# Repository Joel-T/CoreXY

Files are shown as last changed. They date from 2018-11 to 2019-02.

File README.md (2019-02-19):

# Belted Core XY
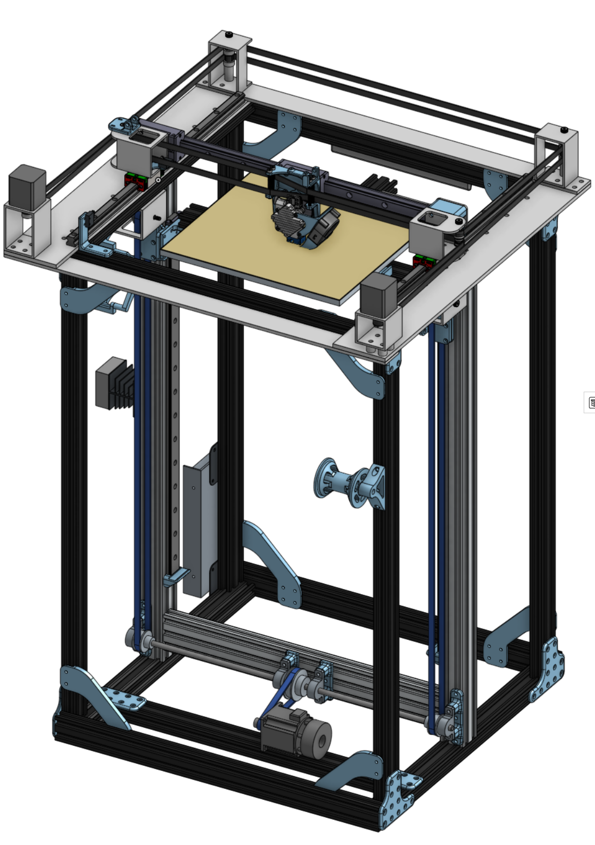
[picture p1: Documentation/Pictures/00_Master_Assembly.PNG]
Core XY Printer Assembly


Documentation, plans, and files  for the Belted Core XY.
## Table of Contents
| Topic  | Resource |
|:---:|:---:|
|Overview|[Link](README.md)  |
|BOM |[Link](Documentation/BOM.md)  |
|Parts |[Link](Parts) |
|Configuration| [Link](Documentation/Configuration.md) |
|Wiring Guide (WIP) | [Link](Documentation/Wiring.md) |
|Write-up| [Link](Documentation/) |

## Overview
The design intent with the Belted Core XY was to create a robust motion platform that can be configured for a number of applications such as 3D printing, light milling, plotting, and laser etching. For the most part it was designed with 3D printing in mind. I plan to completely remodel the Belted Core XY in Fusion when I get the chance so that I can offer more than a step file.
### 3D printer Design Intent:
1. Core XY Kinematics
2. Rigid Frame
3. Ability to change tool
4. Linear rails 
5. Belted bed
6. Z-Stepper w/ brake
7. Aluminum for all major parts of the motion platform
8. Swappable Bed
9. 300mm^2 build plate 
10. 120v AC bed heater

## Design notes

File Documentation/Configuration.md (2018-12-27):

## Configuration for Duet
This section will cover the initial configuration of the Duet controller for the printer, for problems and tuning go [here](Documentation/Issues.md) and for setting up a new Duet [here](https://duet3d.dozuki.com/Guide/1.+Getting+Connected+to+your+Duet/7).

To start we use the [RepRap Config Tool](https://configurator.reprapfirmware.org/Start) to generate the initial configuration file. 

1. First start by selecting the custom configuration option and click next.
2. On this page enable the Read config-override.g option and make sure to select the CoreXY Geometry option. For the axis min and max see the following table: 

| Axis  | Position |
| :--:  | :---: |
| X Min | 0 |
| X Max | 330 |
| Y Min | -40 |
| Y Max | 400 |
| Z Min | 0 |
| Z Max | 550 |

3. On the following page the steppers are configured. The direction is dependent of how you plug the steppers into the Duet so for now just leave them all as Forwards, this can be changed anytime from the web interface or by reversing the plug on the steppers. Note: never insert or remove a stepper while the Duet is powered or you risk frying the driver! For this section I am going to assume 1.8* steppers for the X, Y, and Z, a 0.9* stepper for the E, and x16 microstepping interpolated to x256. The settings are as follows:

| Drive | Steps per mm | Max Speed Change (mm/s) | Max Speed (mm/s) | Acceleration (mm/s<sup>2</sup>) | Motor Current (mA) | Motor Driver |
| :---: | :---: | :---: | :---: | :---: | :---: | :---: |
| X | 80 | 10 | 250 | 500 | 1200 | 0 (X) |
| Y | 80 | 10 | 250 | 500 | 1200 | 1 (Y) |
| Z | 100 | 0.2 | 10 | 20 | 1800 | 2 (Z) |
| E | 837 | 2 | 20 | 250 | 1000 | 3 (E0) |

4. The Z-Probe uses the nozzle itself as the contact there is no X or Y offset so that can be left at 0 mm. For the probe type select the "Smart Effector or Piezo" and set the trigger height to -0.2 mm. This value is how you tune your first layer and like all other settings this can be adjusted later through the web interface. Make sure that it is set as a negative value or after probing your hotend **WILL** crash into the bed. I set the Trigger value to 800 so that if the piezo disk has some pressure on it or there is some electrical interference the probe isn't falsely triggered. Recovery time can be left at 0.4 seconds. The Homing Preferences can also be left at their defaults. Endstop configuration is a pretty straight forward affair. A left-front origin is used and the configuration is as follows:

| Axis | Endstop Type | Endstop Location |
| :--: | :---: | :---: |
| X  |  Active high | At low end |
| Y  |  Active high | At low end |
| Z  | Z-Probe | At low end |

5. The heater settings are simple even with the bed heater being controlled by a SSR. Make sure for the General settings that "Heated Bed" is checked and set to Bang-Bang for control method. For the rest of the heater configuration it is as follows:

| Heater | Type | Temp. Limit | PWM Limit | R25 | β | C | Sensor Channel |
| :----: | :--: | :---: | :---: | :-: | :-:| :-: | :---: |
|  Bed | Heated Bed | 175 | N/A | 100000 | 3950 | 0 | Bed Thermistor |
| E0 | Nozzle | 400 | 100 | N/A | N/A | N/A | MAX31856 on CS1 |

6. On the next page the mesh bed compensation is set up. The print head has a workspace that exceeds the size of the bed so it is important when setting up the mesh leveling that you ensure the probing points are on the bed. For this printer it is as follows:

| X Min | X Max | Y Min | Y Max | Grid Spacing |
| :---: | :---: | :---: | :---: | :---: |
|  15 |  295  |  15 |  295  | 20 |

7. On this page you can name the printer as you see fit and you can also set up the wifi info now to connect to the network that the printer will be on. I advise that after the Duet is setup and configured to go into your router and assign the Duet a fixed IP so that you can easily make a bookmark to the web interface.
8. For the final page we will be configuring the cooling fans and the z axis brake. There should be three fans, 0, 1, and 2, if there isn't just click the add fan button in the upper right. Fan 0 will be the part cooling fan, fan 1 the hotend fan, and fan 2 the brake. This is set up as such:

| Name | Value | Inverted | Frequency | Thermostatic Control | Monitored Heaters | Thermostatic Mode Trigger Temp. |
| :--: | :---: | :---: | :---: | :---: | :---: | :---: |
| Fan0 | 0 | No | 500 | No | N/A | N/A |
| Fan1 |  100  | No | 500 | Yes | E0 | 45 |
| Fan2 | 0 | No | 500 | No | N/A | N/A |

9. Finally click finish and download the bundle as a zip file.

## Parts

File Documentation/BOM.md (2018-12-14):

## Bill of Materials

|  | Part Name | Number Needed |
|:---:|:---:|:---:|
| 2040 Extrusion |  |  |
|  | 210mm | 1 |
|  | 415mm | 1 |
|  | 470mm | 1 |
|  | 500mm | 8 |
|  | 550mm | 8 |
|  | 800mm | 4 |
| 2060 Extrusion |  |  |
|  | 470mm | 1 |
| 4040 Extrusion |  |  |
|  | 800mm | 2 |
| Aluminum Plate |  |  |
|  | 3.5" x 24" x 1/4" | 2 |
|  | 40mm x 48" x 5mm | 2 |
|  | 12" x 12" x 3/8" Mic6 | 1 |
|Aluminum Tubing|  |  |
|  | 2" x 2" x 24" | 1 |
|  | 2" x 3" x 12" | 1 |
| Linear Rails |  |  |
|  | HGH 15 | 2 |
|  | HGH 20 | 1 |
|  | MGW 12 | 2 |
| Linear Rail Block |  |  |
|  | HGH 15 Square Low | 2 |
|  | HGH 20 Square Low | 2 |
|  | MGW 12 Long | 2 |
| Hardware |  |  |
|  | M4 Drop in nut | 72 |
|  | M5 Drop in nut | 24 |
|  | M4 LP nut | 1 pack |
|  | M5 LP nut | 1 pack |
|  | M6 LP nut | 4 |
|  | M6 nut | 22 |
|  | M8 LP nut | 2 |
|  | M2 x 12mm | 4 |
|  | M3 x 8mm | 8 |
|  | M3 x 12mm | 2 |
|  | M4 x 8mm | 72 |
|  | M4 x 10mm | 32 |
|  | M4 x 16mm | 30 |
|  | M4 x 45mm | 4 |
|  | M5 x 8mm | 5 |
|  | M5 x 10mm | 44 |
|  | M5 x 12mm | 12 |
|  | M6 x 16mm | 6 |
|  | M6 x 35mm | 16 |
|  | M6 x 45mm | 2 |
|  | M8 x 25mm | 2 |
|  | 1/4" Shoulder Screw 2" Shoulder | 4 |
|  | 1/4" Shoulder Screw 3-1/4" Shoulder | 2 |
|  | 10-24 Thin Nut | 6 |
|  | GT2 20 Tooth 9mm Belt 5mm Bore | 2 |
|  | GT2 20 Tooth 9mm Belt 6.35mm Bore | 6 |
|  | 1/2" Flange Bearing | 4 |
|  | M8 Rod 550mm | 1 |
|  | M8 Pillow Bearing | 4 |
|  | HTD 3M 16 Tooth 8mm Bore | 1 |
|  | HTD 3M 32 Tooth 8mm Bore | 2 |
|  | HTD 3M 48 Tooth 8mm Bore | 1 |
|  | HTD 3M 32 Tooth 6.35mm Bore | 2 |
|  | L Bracket Triple | 2 |
|  | Hidden Tee Nut | 28 |
|  | Spacer 6mm Bore 13mm Length | 4 |
|  | Spacer 6mm Bore 25mm Length | 4 |
|  | Spacer 1/4" Bore 1/2" Length | 4 |
|  | Spacer 1/4" Bore 1" Length | 2 |
|  | Thrust Bearing 1/4" Bore 5/8" OD 1/16" Thick | 10 |
|  | 608 Bearing | 2-4 |
|  | Titan Aero | 1 |
| Electronics |  |  |
|  | Duet | 1 |
|  | PT100 Daughter Board | 1 |
|  | Piezo20 or Universal Kit | 1 |
|  | Nema 17 Stepper 0.9* LP | 1 |
|  | Nema 17 Stepper 1.8* | 2 |
|  | Nema 23 Stepper w/ Brake | 1 |
|  | AC SSR | 1 |
|  | 4020 Blower Fan | 1 |
|  | Meanwell 350W PSU | 1 |
|  | Cooling Fan | 1 |
|  | NC Micro Switch | 2 |
| Printed Parts |  |  |
|  | Chain Link Pair | 18 |
|  | Corner Bracket | 4 |
|  | Corner Bracket Mirror | 4 |
|  | Corner Plate | 4 |
|  | Corner Pate Mirror | 4 |
|  | Bed Mount | 2 |
|  | Duet Fan Mount | 2 |
|  | Pillow Block Wide | 2 |
|  | Pillow Block Narrow | 2 |
|  | Straight Plate | 2 |
|  | Bed Stop | 2 |
|  | Fixed Bed Belt Clamp | 2 |
|  | Ribbed Bed Belt Clamp | 2 |
|  | Bed Thumb Screw | 2 |
|  | Bed Leveler | 2 |
|  | Spool Bearing | 2 |
|  | Bed Mount Wide | 1 |
|  | Rail Z Bed Left | 1 |
|  | Rail Z Bed Right | 1 |
|  | X Endstop | 1 |
|  | Y Endstop | 1 |
|  | Tube Mount | 1 |
|  | Cable Chain Hotend | 1 |
|  | Cable Chain Tubing | 1 |
|  | Hotend Fan | 1 |
|  | Titan Areo | 1 |
|  | Duet Board Mount | 1 |
|  | Nema 23 Mount | 1 |

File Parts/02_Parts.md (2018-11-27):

## Parts
All Parts are stored here for download. The Chainlink pair file is from the Maker's Tool Works Minimax 3D printer files, all other parts are my design. See the [BOM](Documentation/01_BOM.md) for the number of each part that is needed.

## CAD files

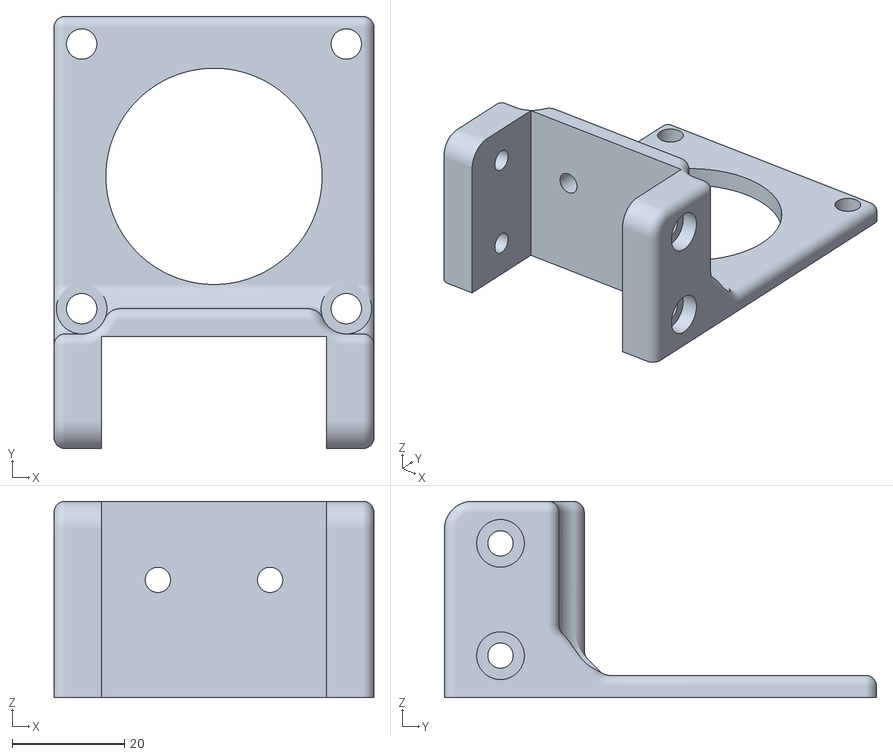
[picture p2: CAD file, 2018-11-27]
Parts/STL/Nema 23 mount.stl
57.0 x 77.0 x 35.0

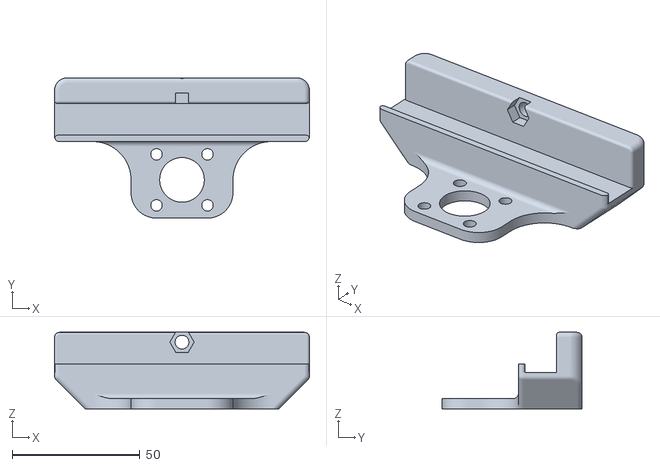
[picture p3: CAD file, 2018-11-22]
Parts/STL/Bed Mount Wide.stl
100.0 x 55.0 x 30.0

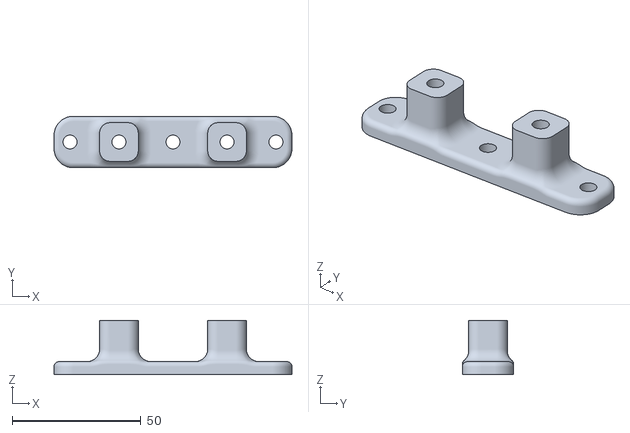
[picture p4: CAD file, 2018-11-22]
Parts/STL/Pillow Block Wide.stl
92.5 x 20.0 x 21.0

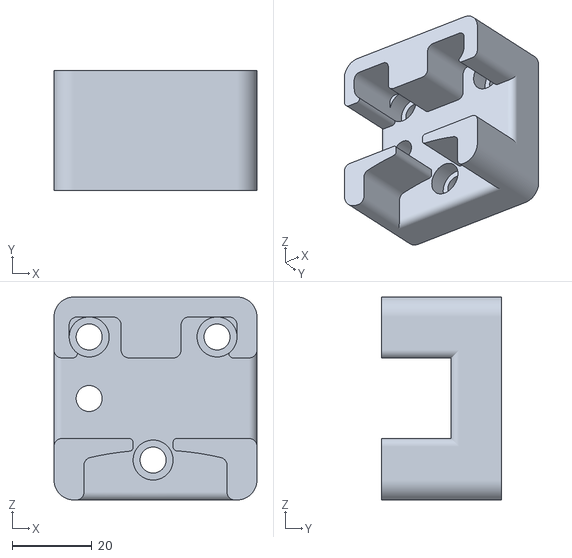
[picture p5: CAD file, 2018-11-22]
Parts/STL/Tubing Mount.stl
50.8 x 30.0 x 50.8

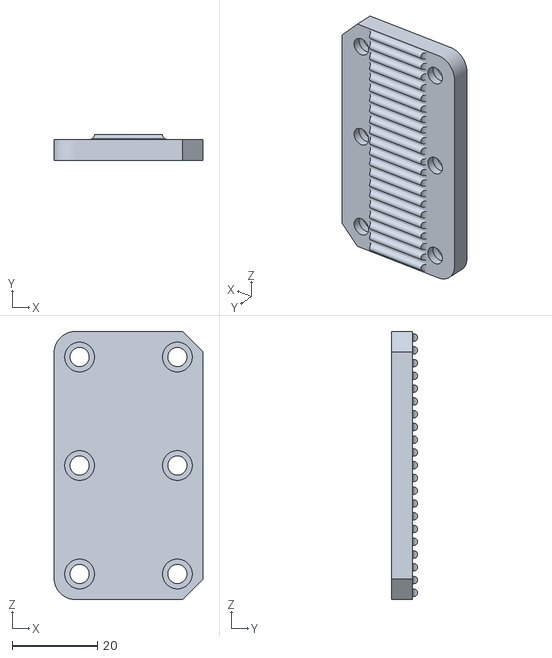
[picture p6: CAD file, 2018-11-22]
Parts/STL/Ribbed Clamp.stl
35.0 x 6.17 x 63.0

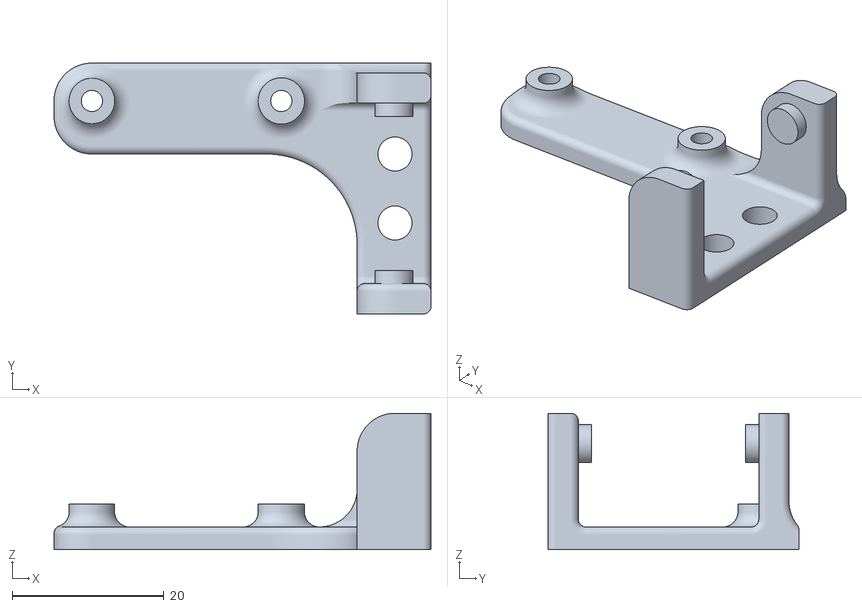
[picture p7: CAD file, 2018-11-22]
Parts/STL/Cable Chain Hotend.stl
49.8 x 33.1 x 18.0

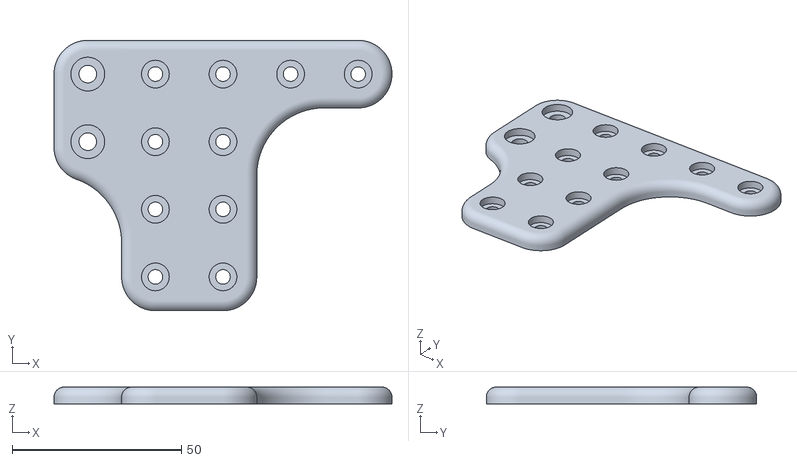
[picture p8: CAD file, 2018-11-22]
Parts/STL/Corner Plate Mirror.stl
100.0 x 80.0 x 5.00

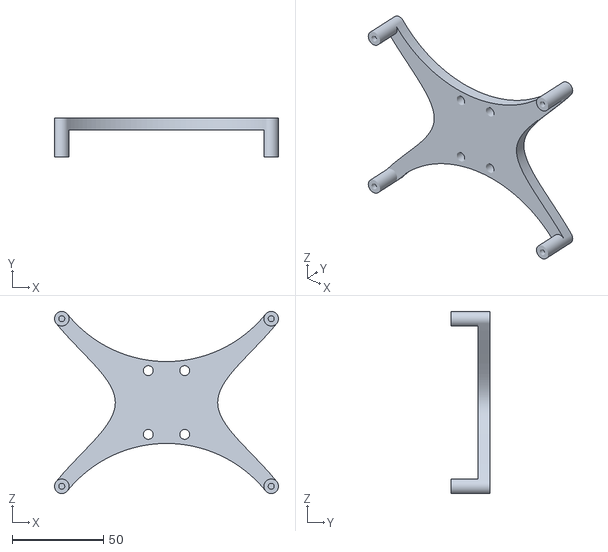
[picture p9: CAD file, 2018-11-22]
Parts/STL/Duet Mount.stl
123.0 x 21.5 x 100.0

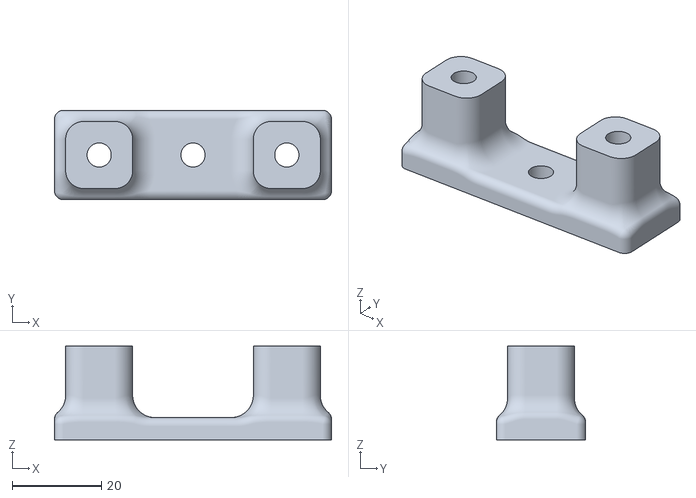
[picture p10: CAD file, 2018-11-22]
Parts/STL/Pillow Block Narrow.stl
62.0 x 20.0 x 21.0

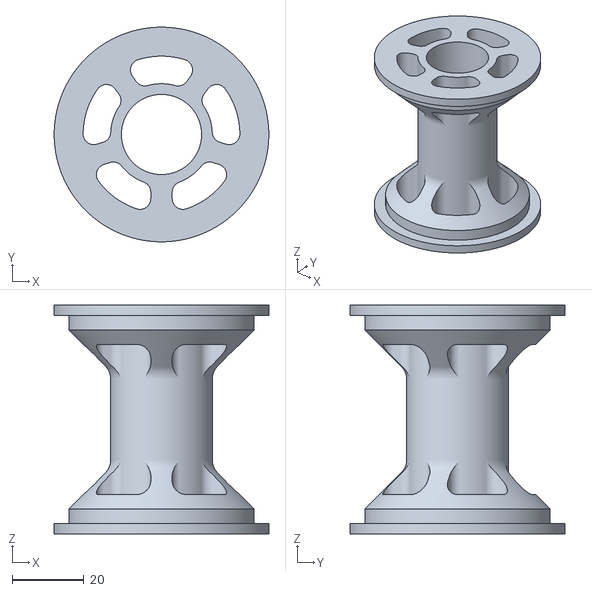
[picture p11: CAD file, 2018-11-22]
Parts/STL/Filament Bearing.stl
60.0 x 60.0 x 64.0

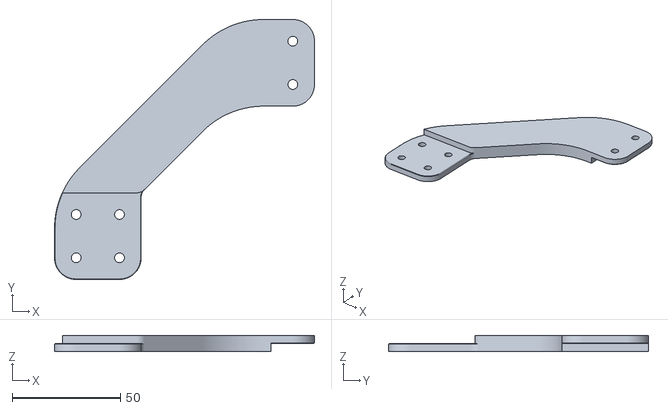
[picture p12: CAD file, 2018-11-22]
Parts/STL/Corner Bracket Mirror.stl
120.0 x 120.0 x 7.50

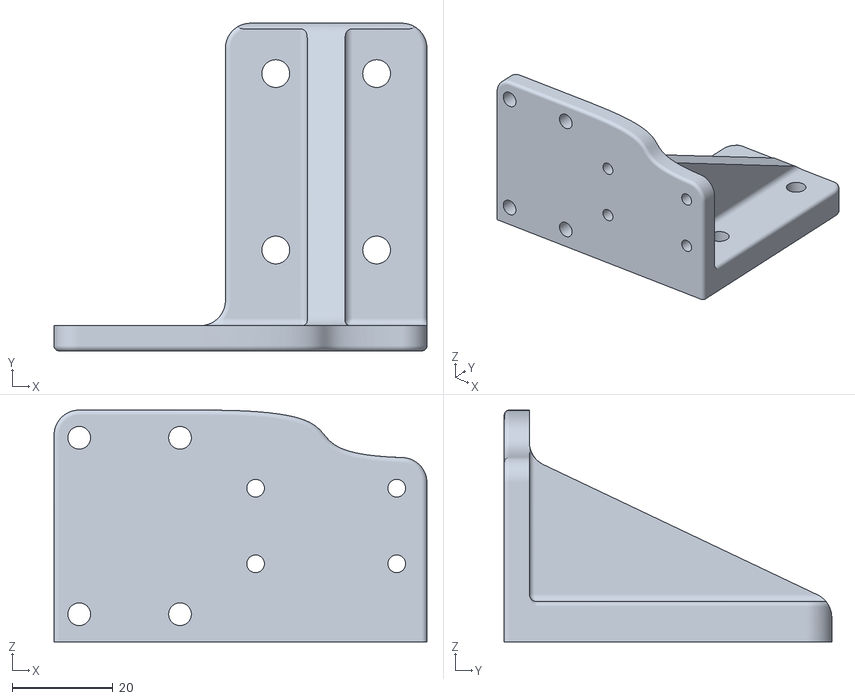
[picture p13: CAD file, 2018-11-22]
Parts/STL/Rail Z Bed Mount Right.stl
74.0 x 65.0 x 46.0

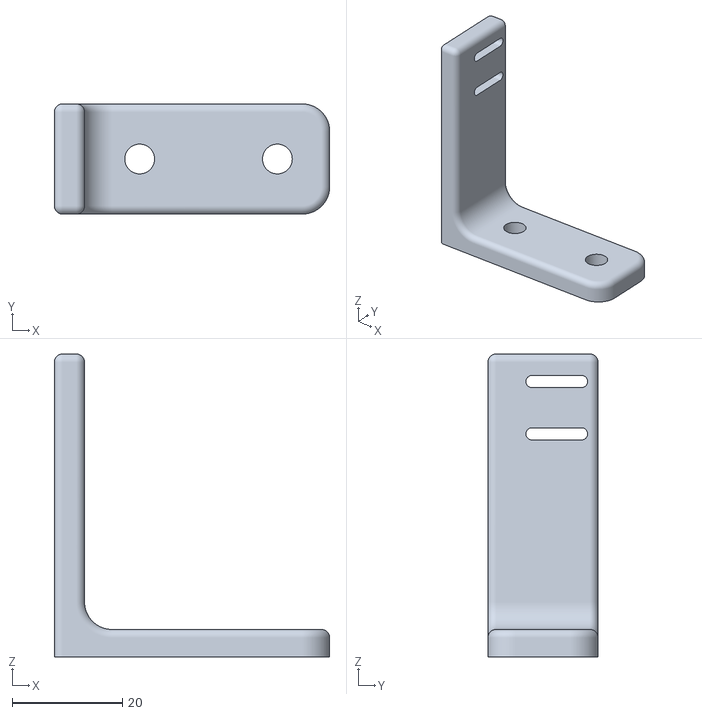
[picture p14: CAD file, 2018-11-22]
Parts/STL/Y End Stop.stl
50.0 x 20.0 x 55.0

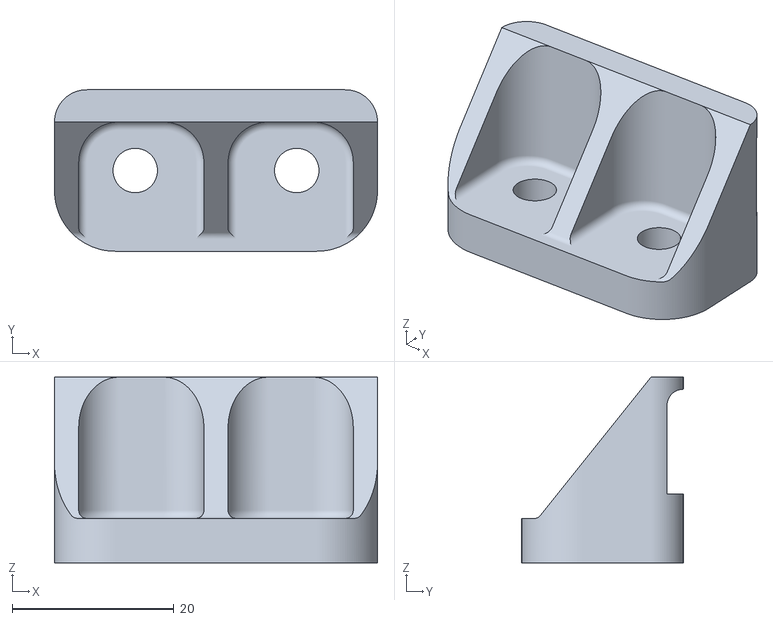
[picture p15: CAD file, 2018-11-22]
Parts/STL/Bed Stop.stl
40.0 x 20.0 x 23.0

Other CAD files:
Parts/STL/Corner Bracket.stl
Parts/STL/Corner Plate.stl
Parts/STL/Hotend Fan Mount.stl
Parts/STL/Bed Mount.stl
Parts/STL/Cable Chain Tubing.stl
Parts/STL/Duet Fan Mount.stl
Parts/STL/Fixed Clamp.stl
Parts/STL/Leveler.stl
Parts/STL/Rail Z Bed Mount Left.stl
Parts/STL/Screw Head.stl
Parts/STL/X End Stop.stl
Parts/STL/chainlink pair.STL

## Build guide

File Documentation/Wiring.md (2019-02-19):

## Wiring

This section will cover wiring up all of the electronics for the printer as well as any other accessories such as lights and fans.

### Overview
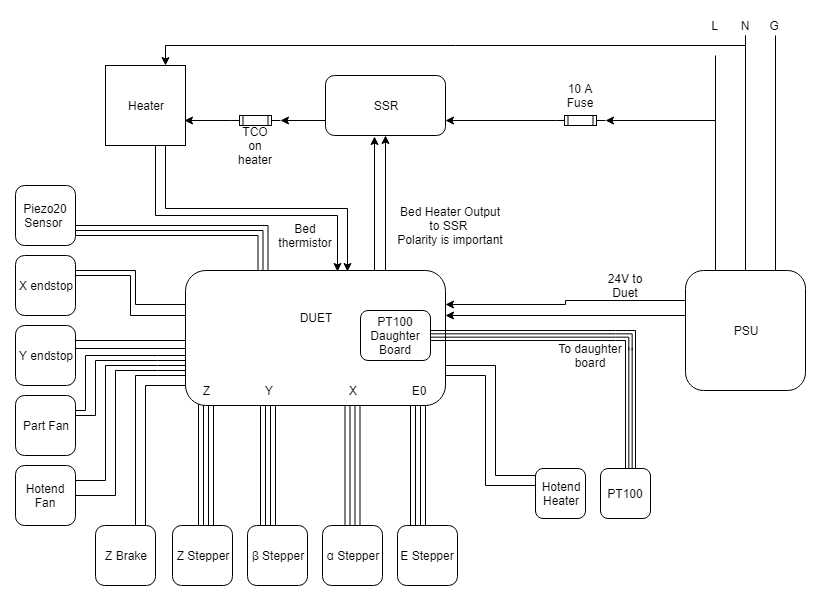
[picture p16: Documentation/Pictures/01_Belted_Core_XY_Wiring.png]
Core XY Printer Wiring


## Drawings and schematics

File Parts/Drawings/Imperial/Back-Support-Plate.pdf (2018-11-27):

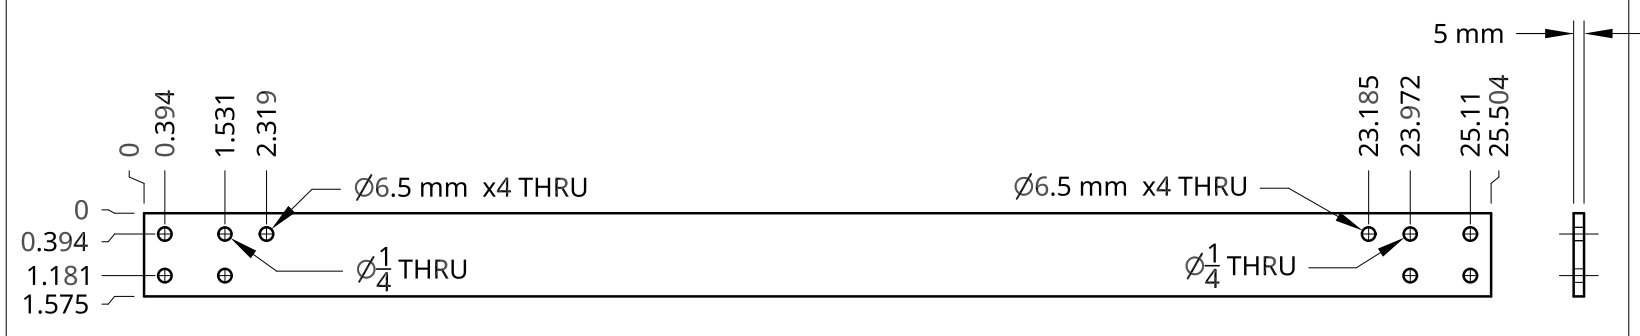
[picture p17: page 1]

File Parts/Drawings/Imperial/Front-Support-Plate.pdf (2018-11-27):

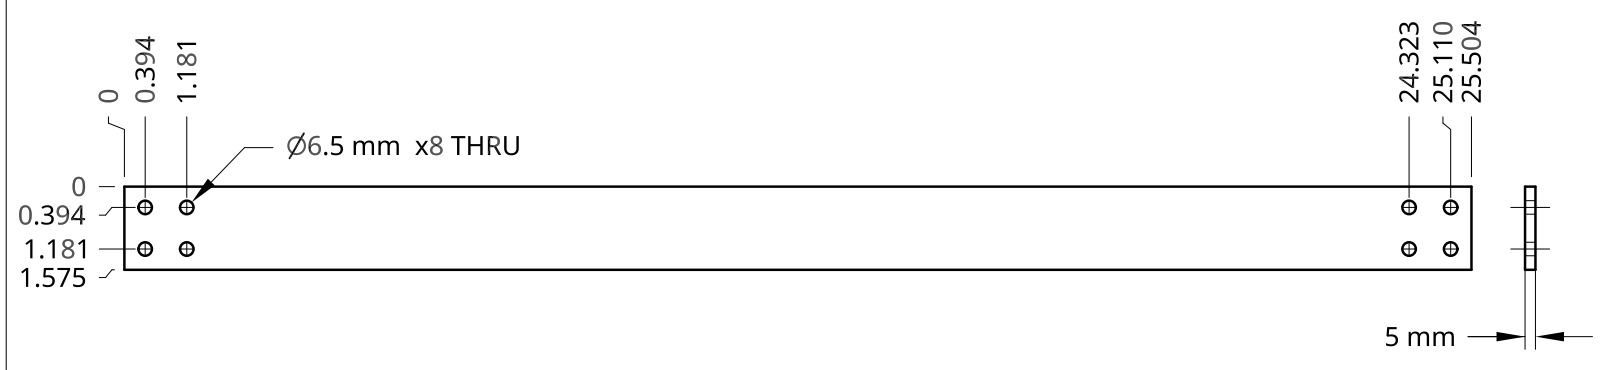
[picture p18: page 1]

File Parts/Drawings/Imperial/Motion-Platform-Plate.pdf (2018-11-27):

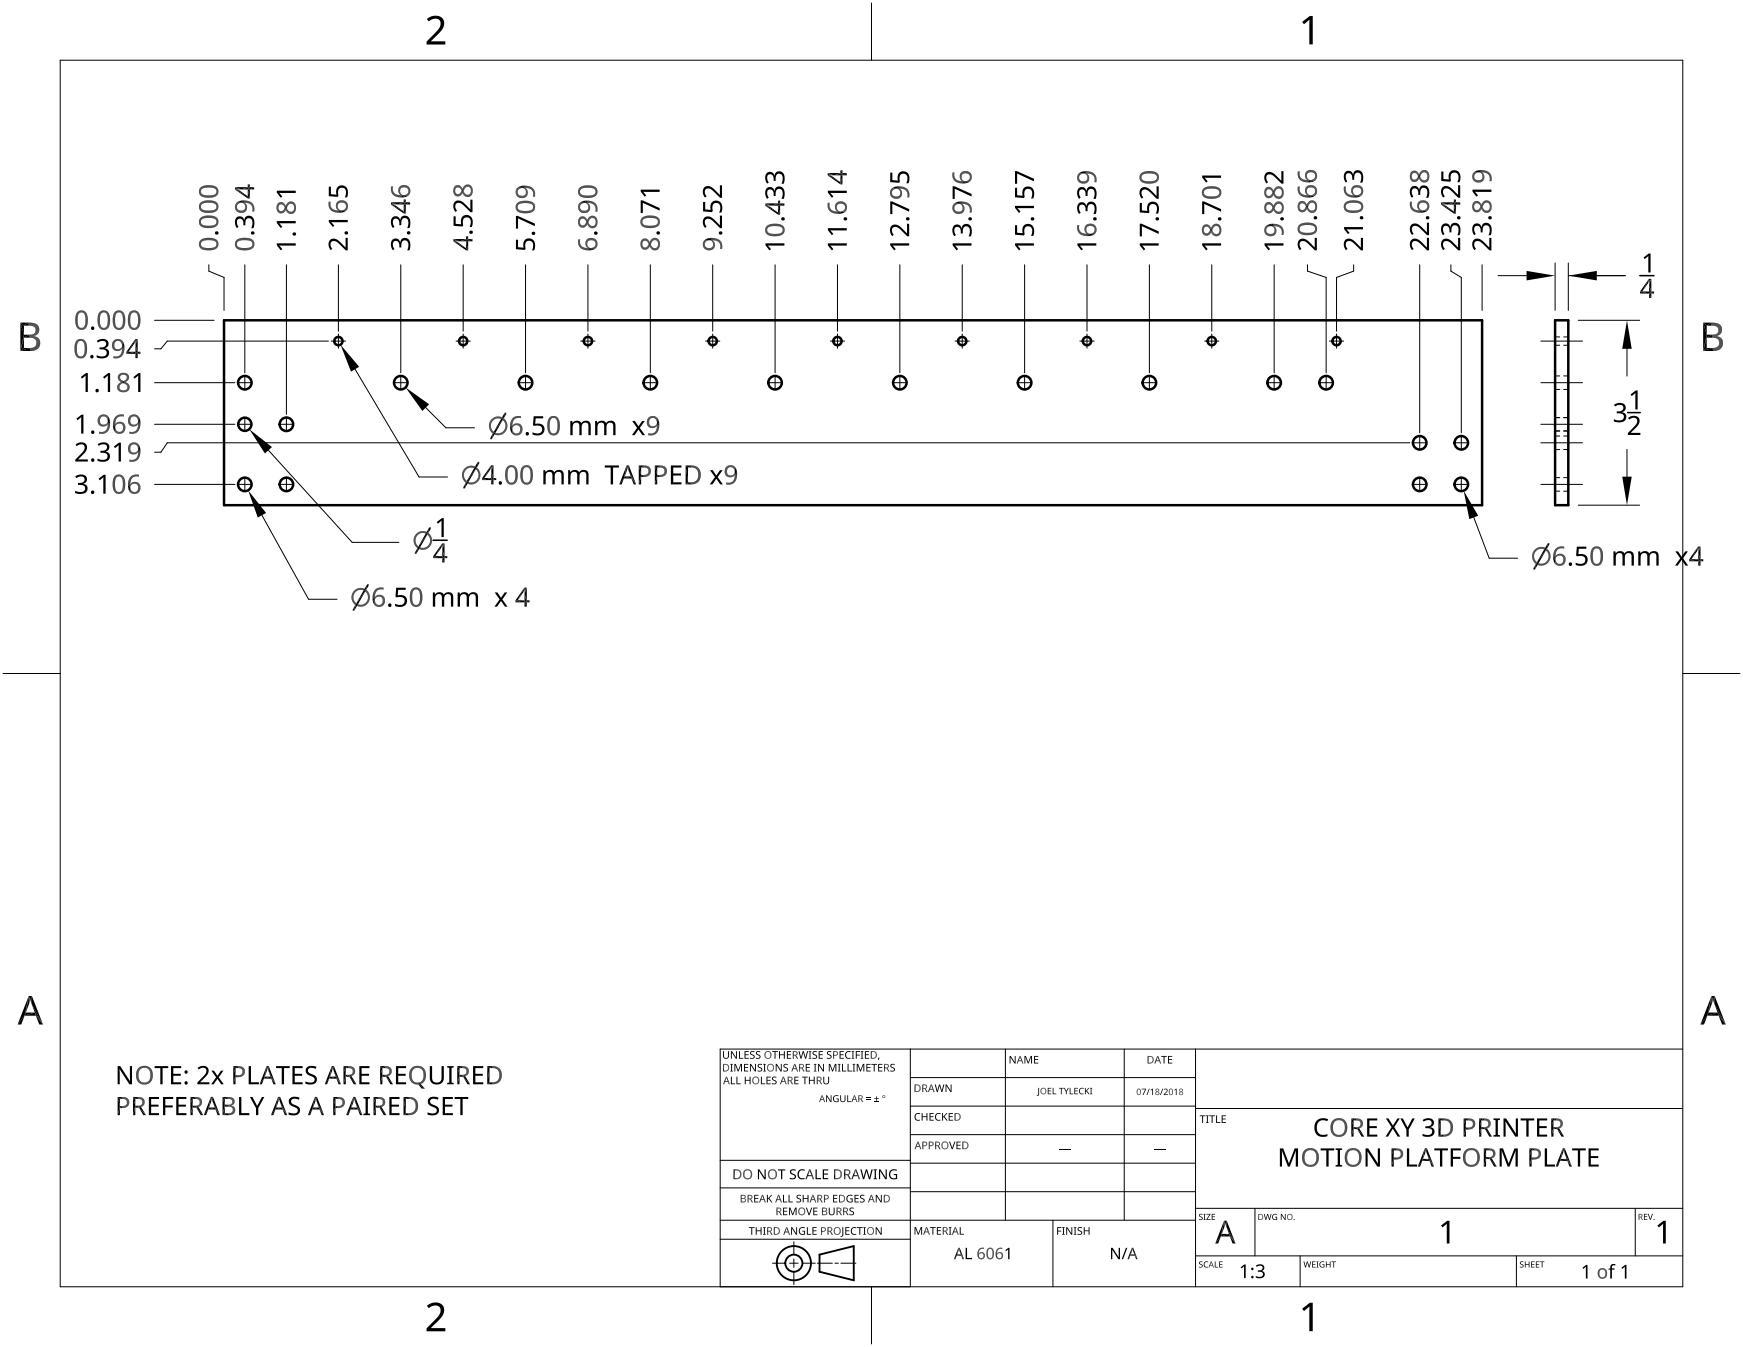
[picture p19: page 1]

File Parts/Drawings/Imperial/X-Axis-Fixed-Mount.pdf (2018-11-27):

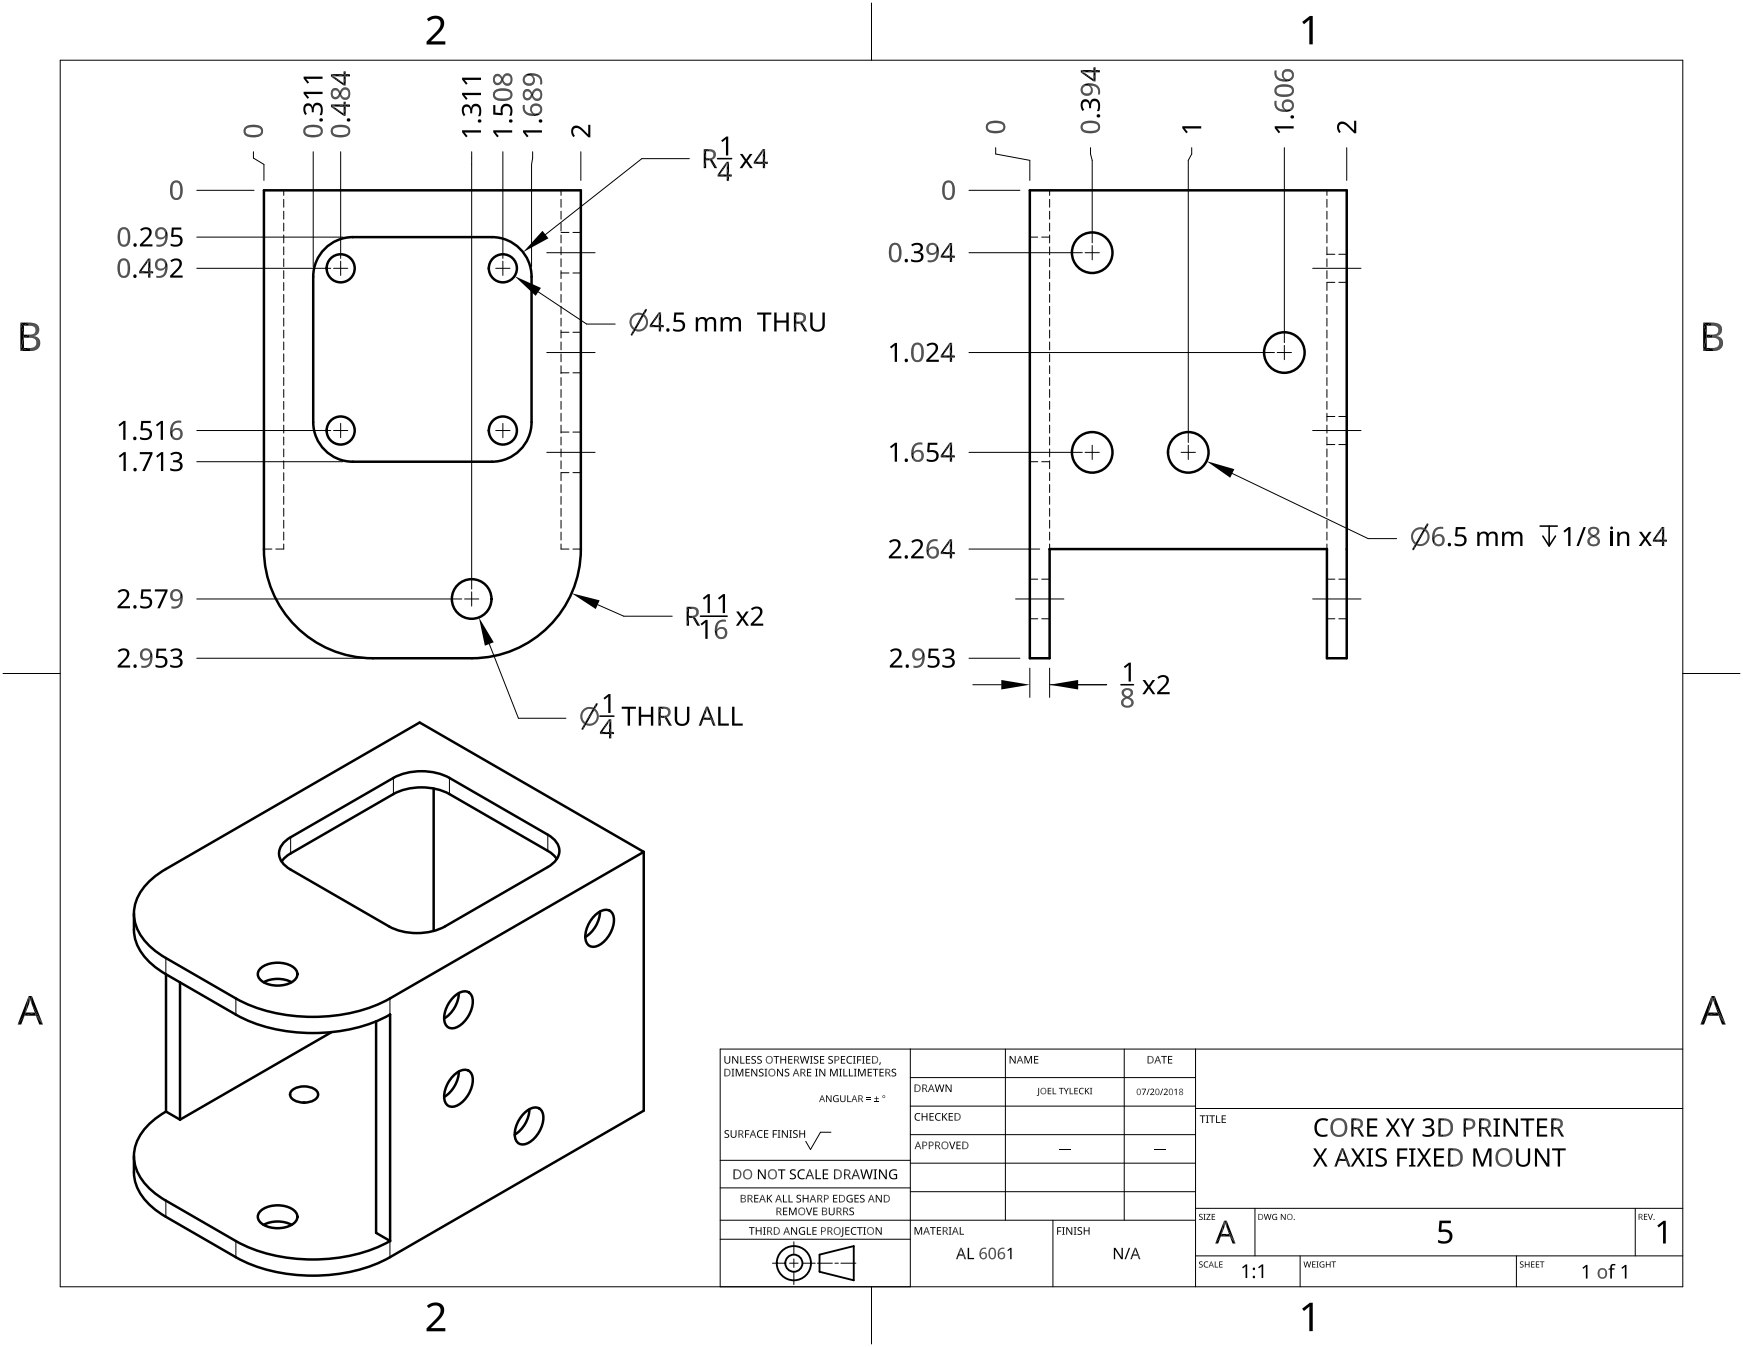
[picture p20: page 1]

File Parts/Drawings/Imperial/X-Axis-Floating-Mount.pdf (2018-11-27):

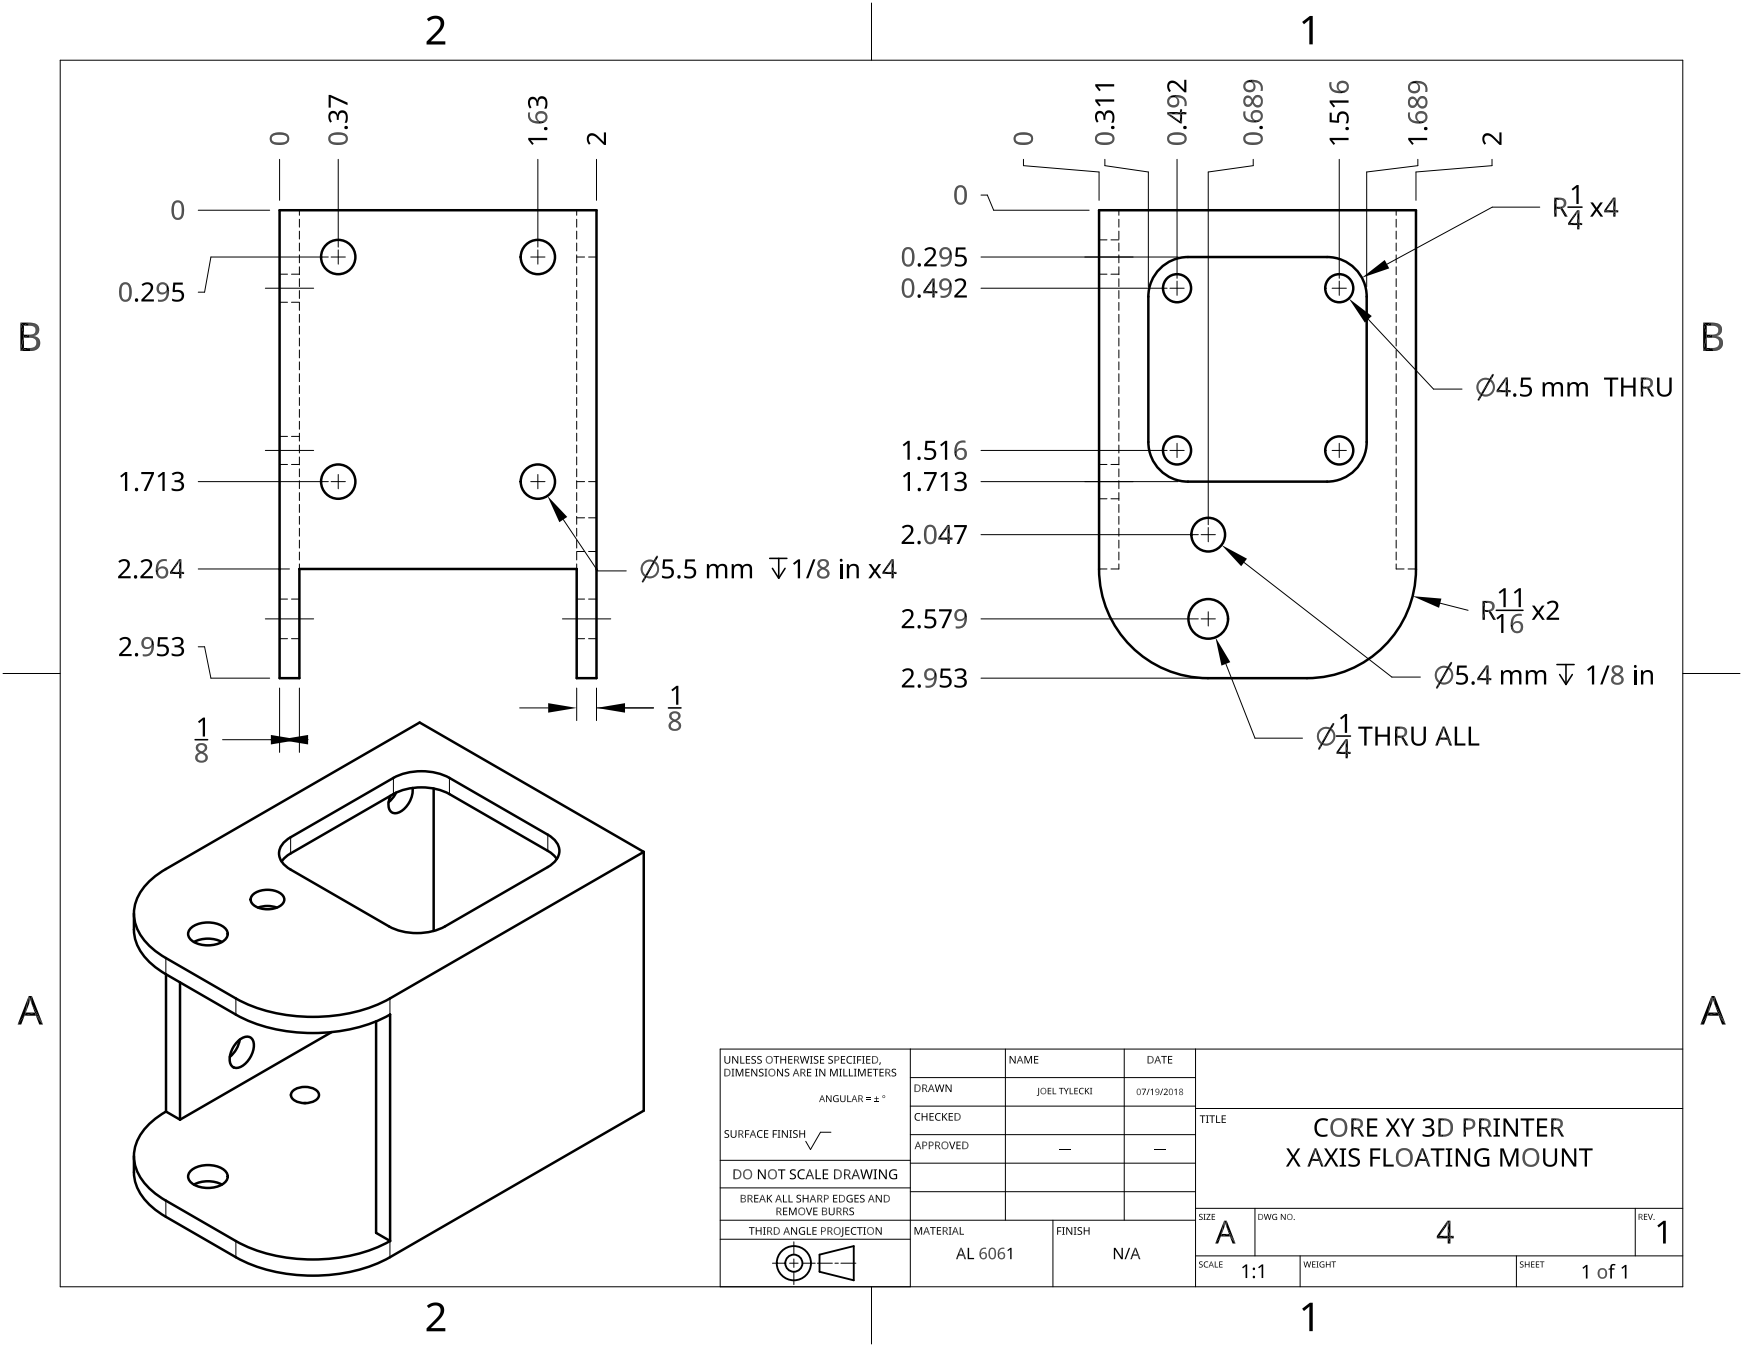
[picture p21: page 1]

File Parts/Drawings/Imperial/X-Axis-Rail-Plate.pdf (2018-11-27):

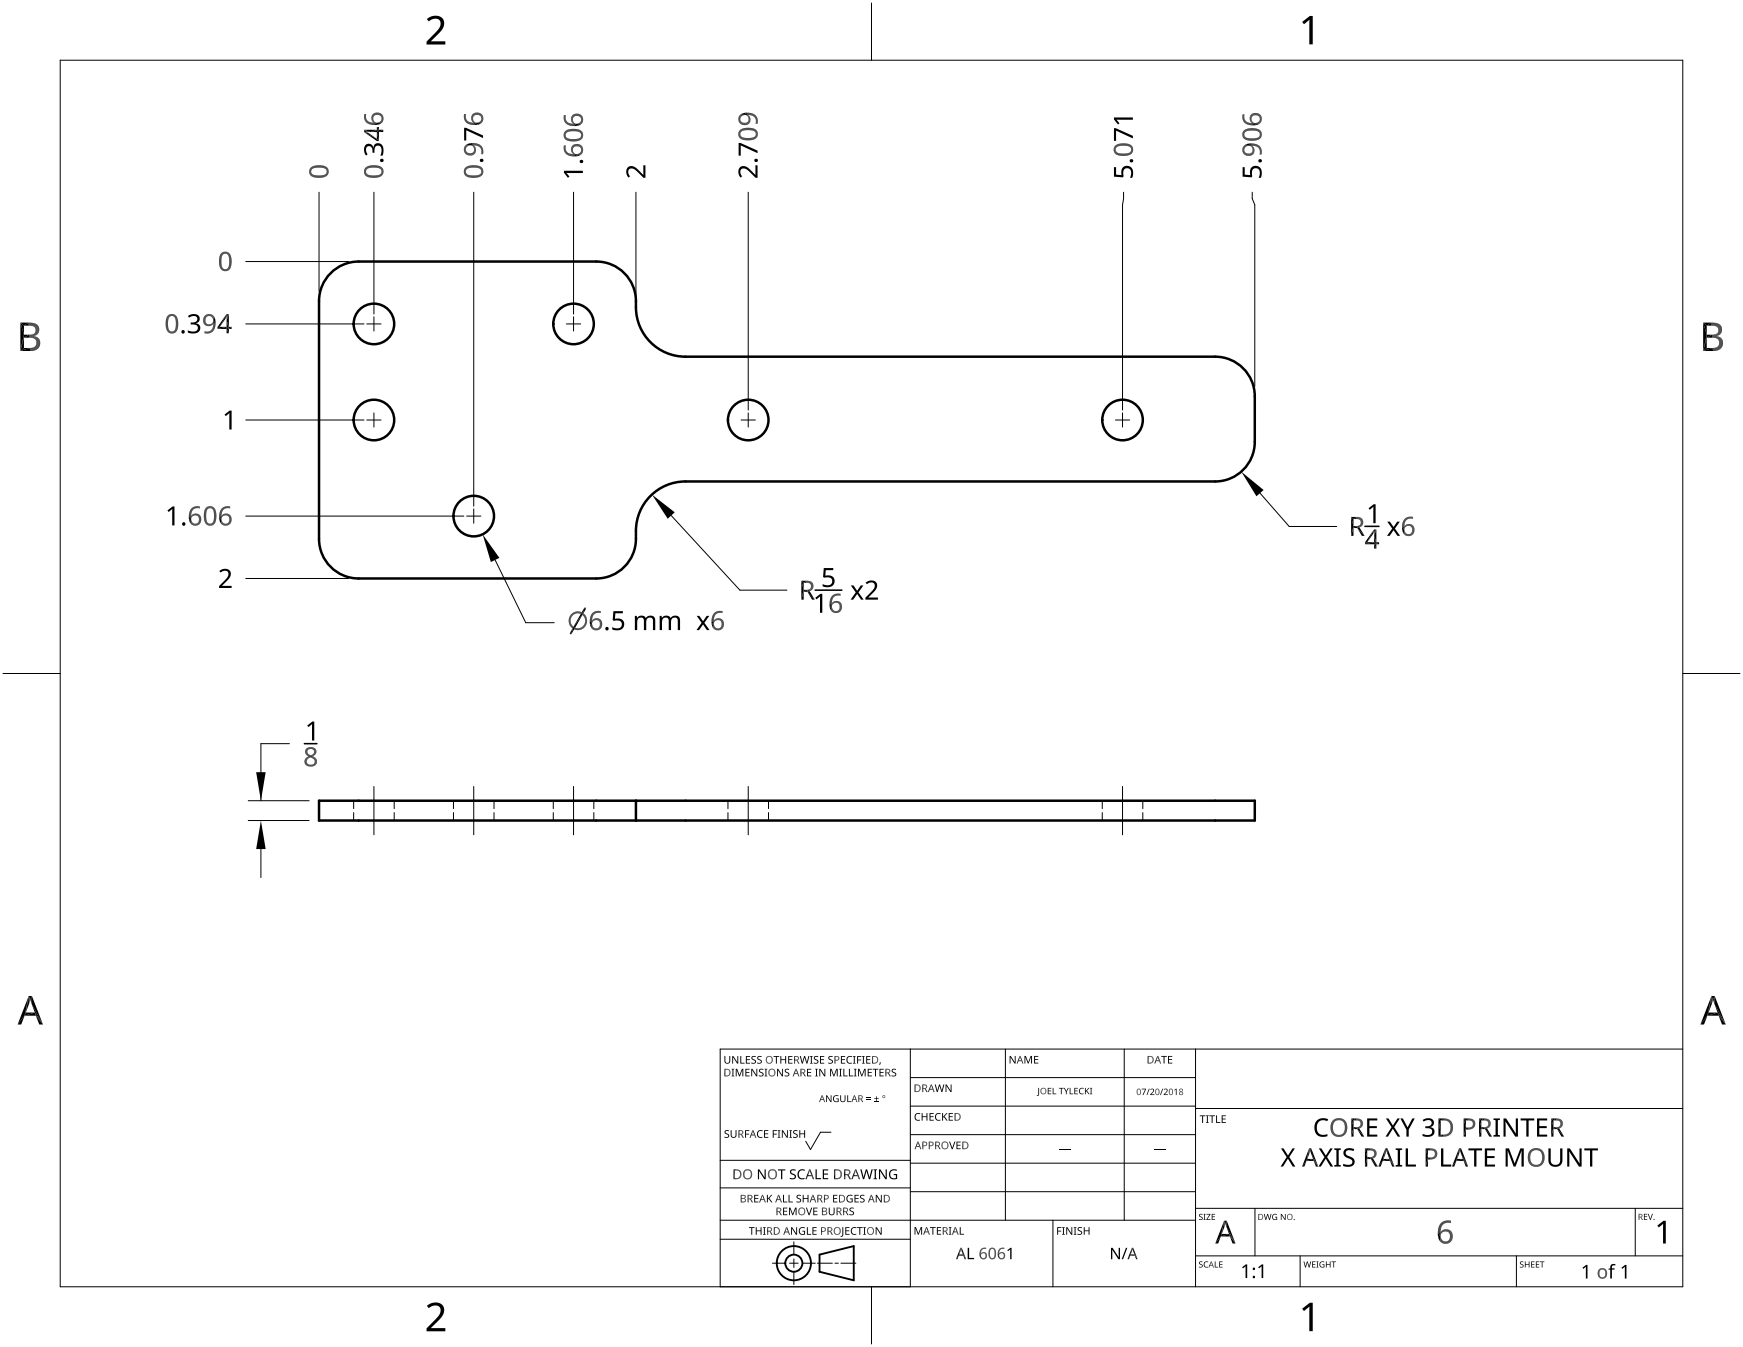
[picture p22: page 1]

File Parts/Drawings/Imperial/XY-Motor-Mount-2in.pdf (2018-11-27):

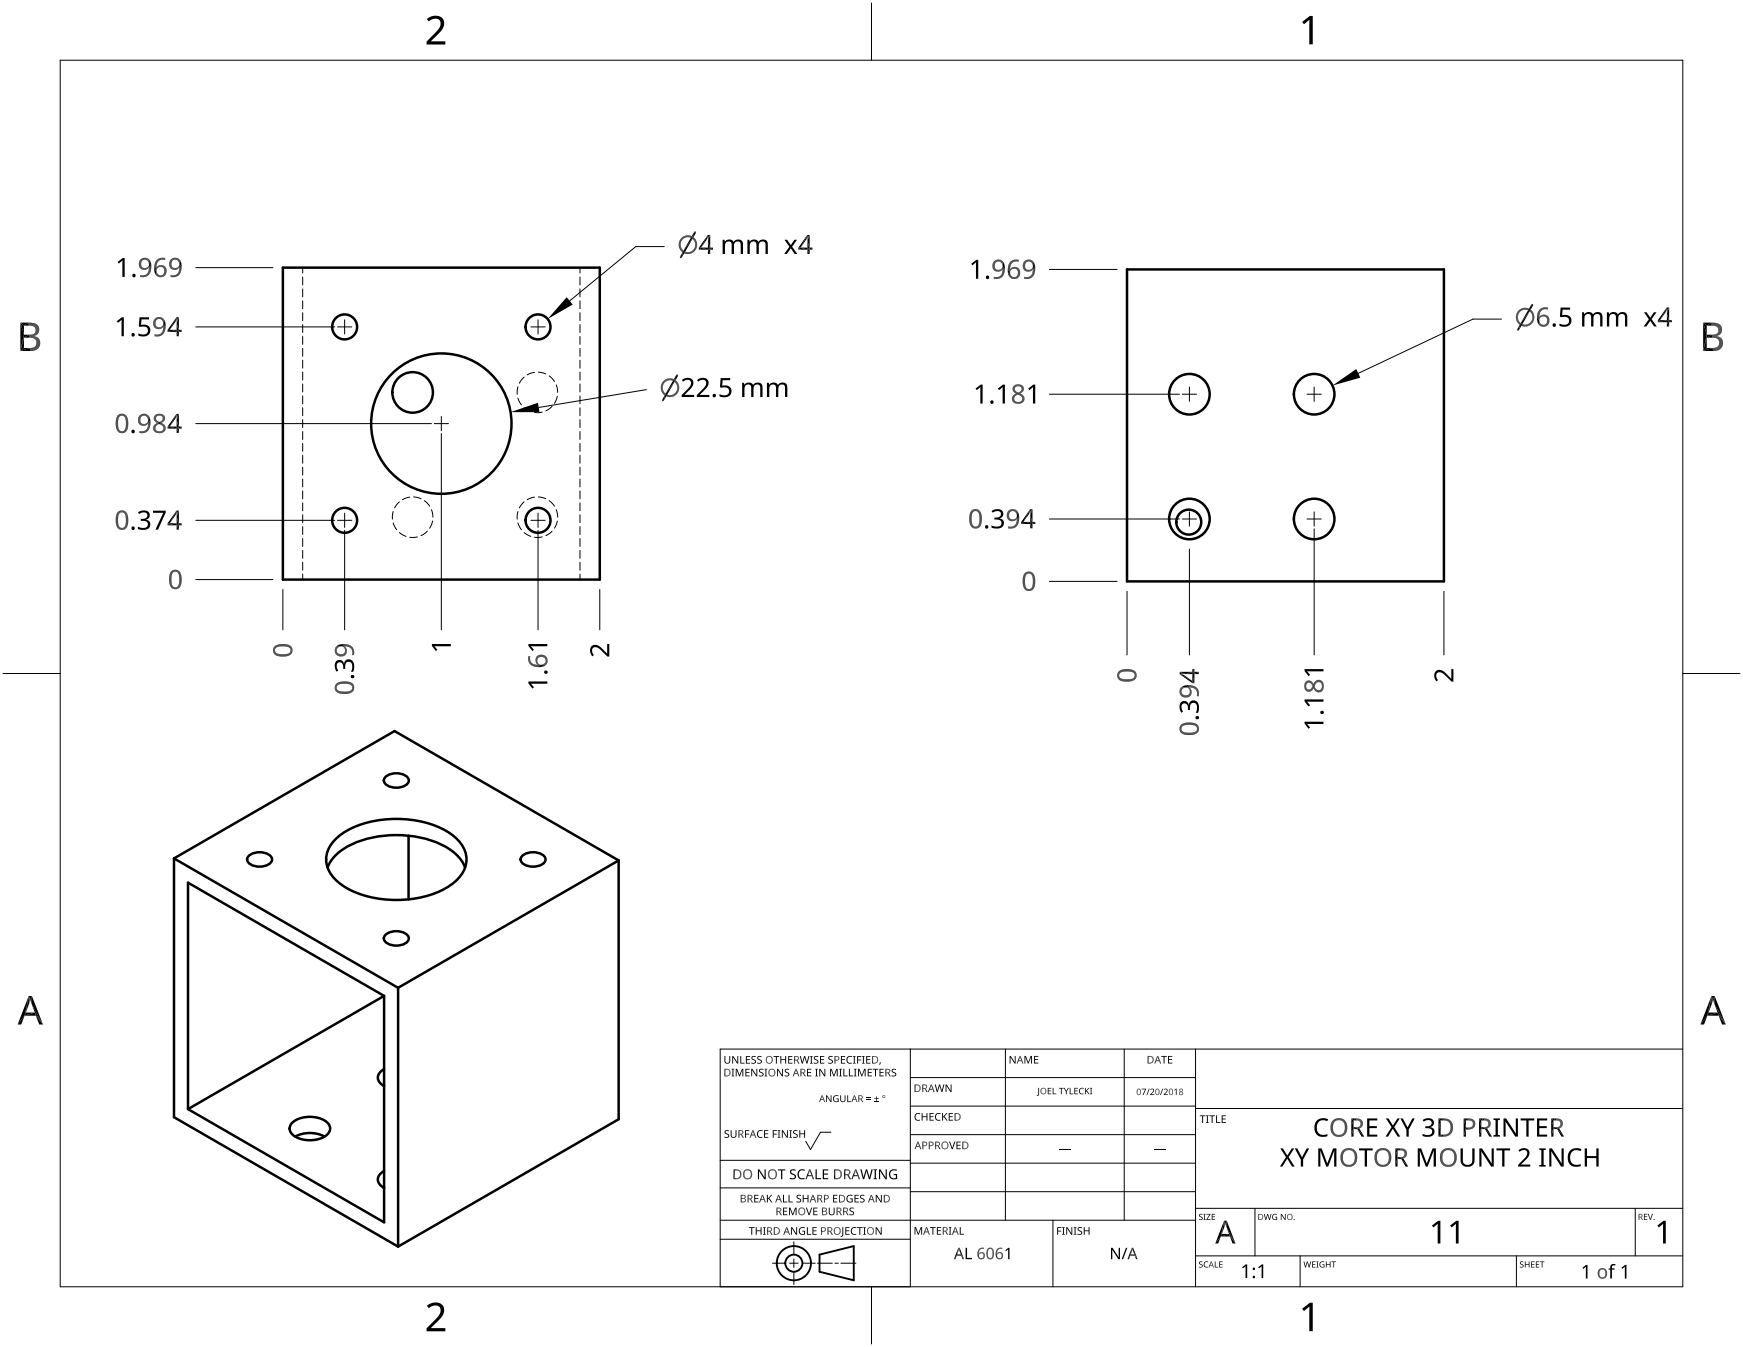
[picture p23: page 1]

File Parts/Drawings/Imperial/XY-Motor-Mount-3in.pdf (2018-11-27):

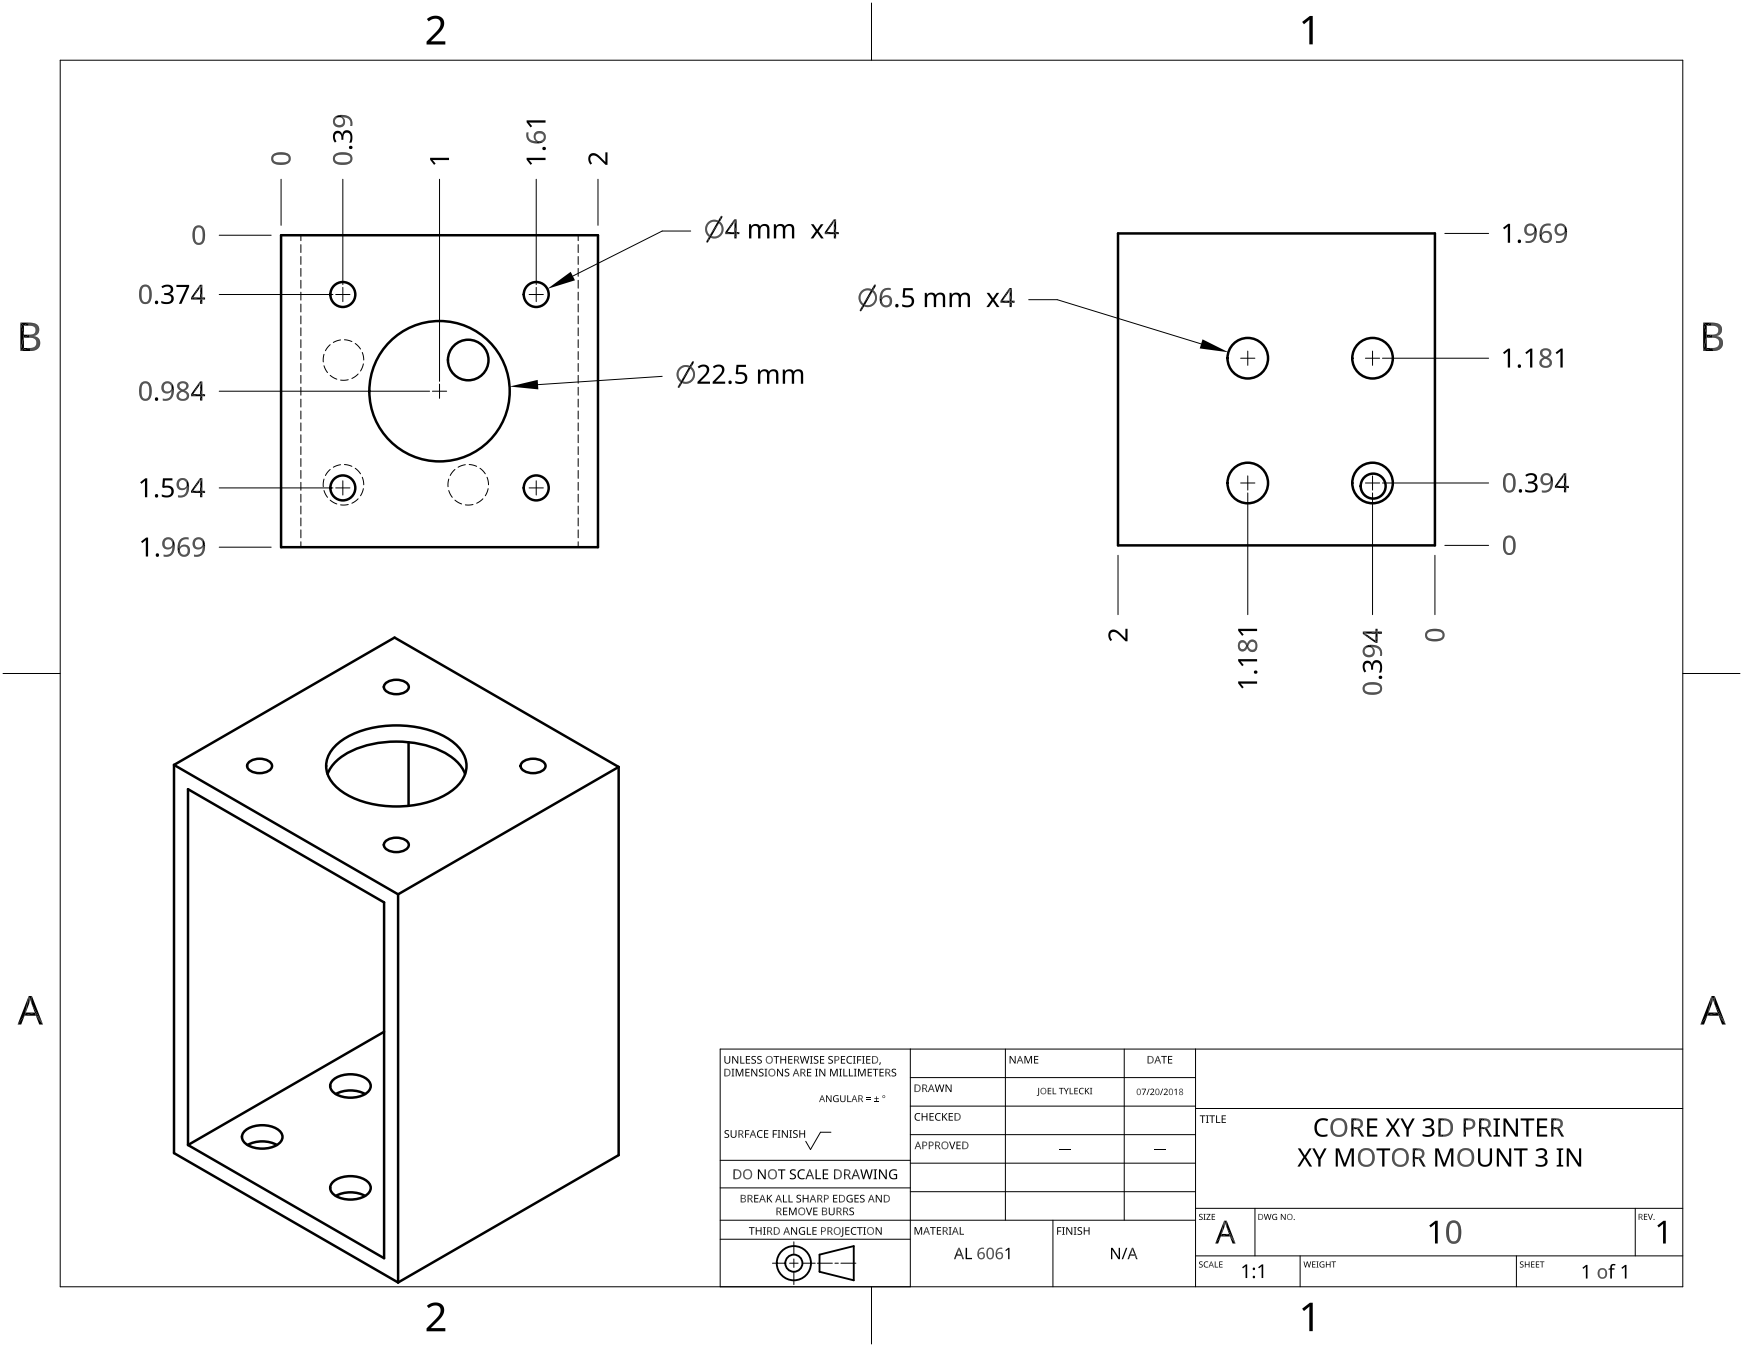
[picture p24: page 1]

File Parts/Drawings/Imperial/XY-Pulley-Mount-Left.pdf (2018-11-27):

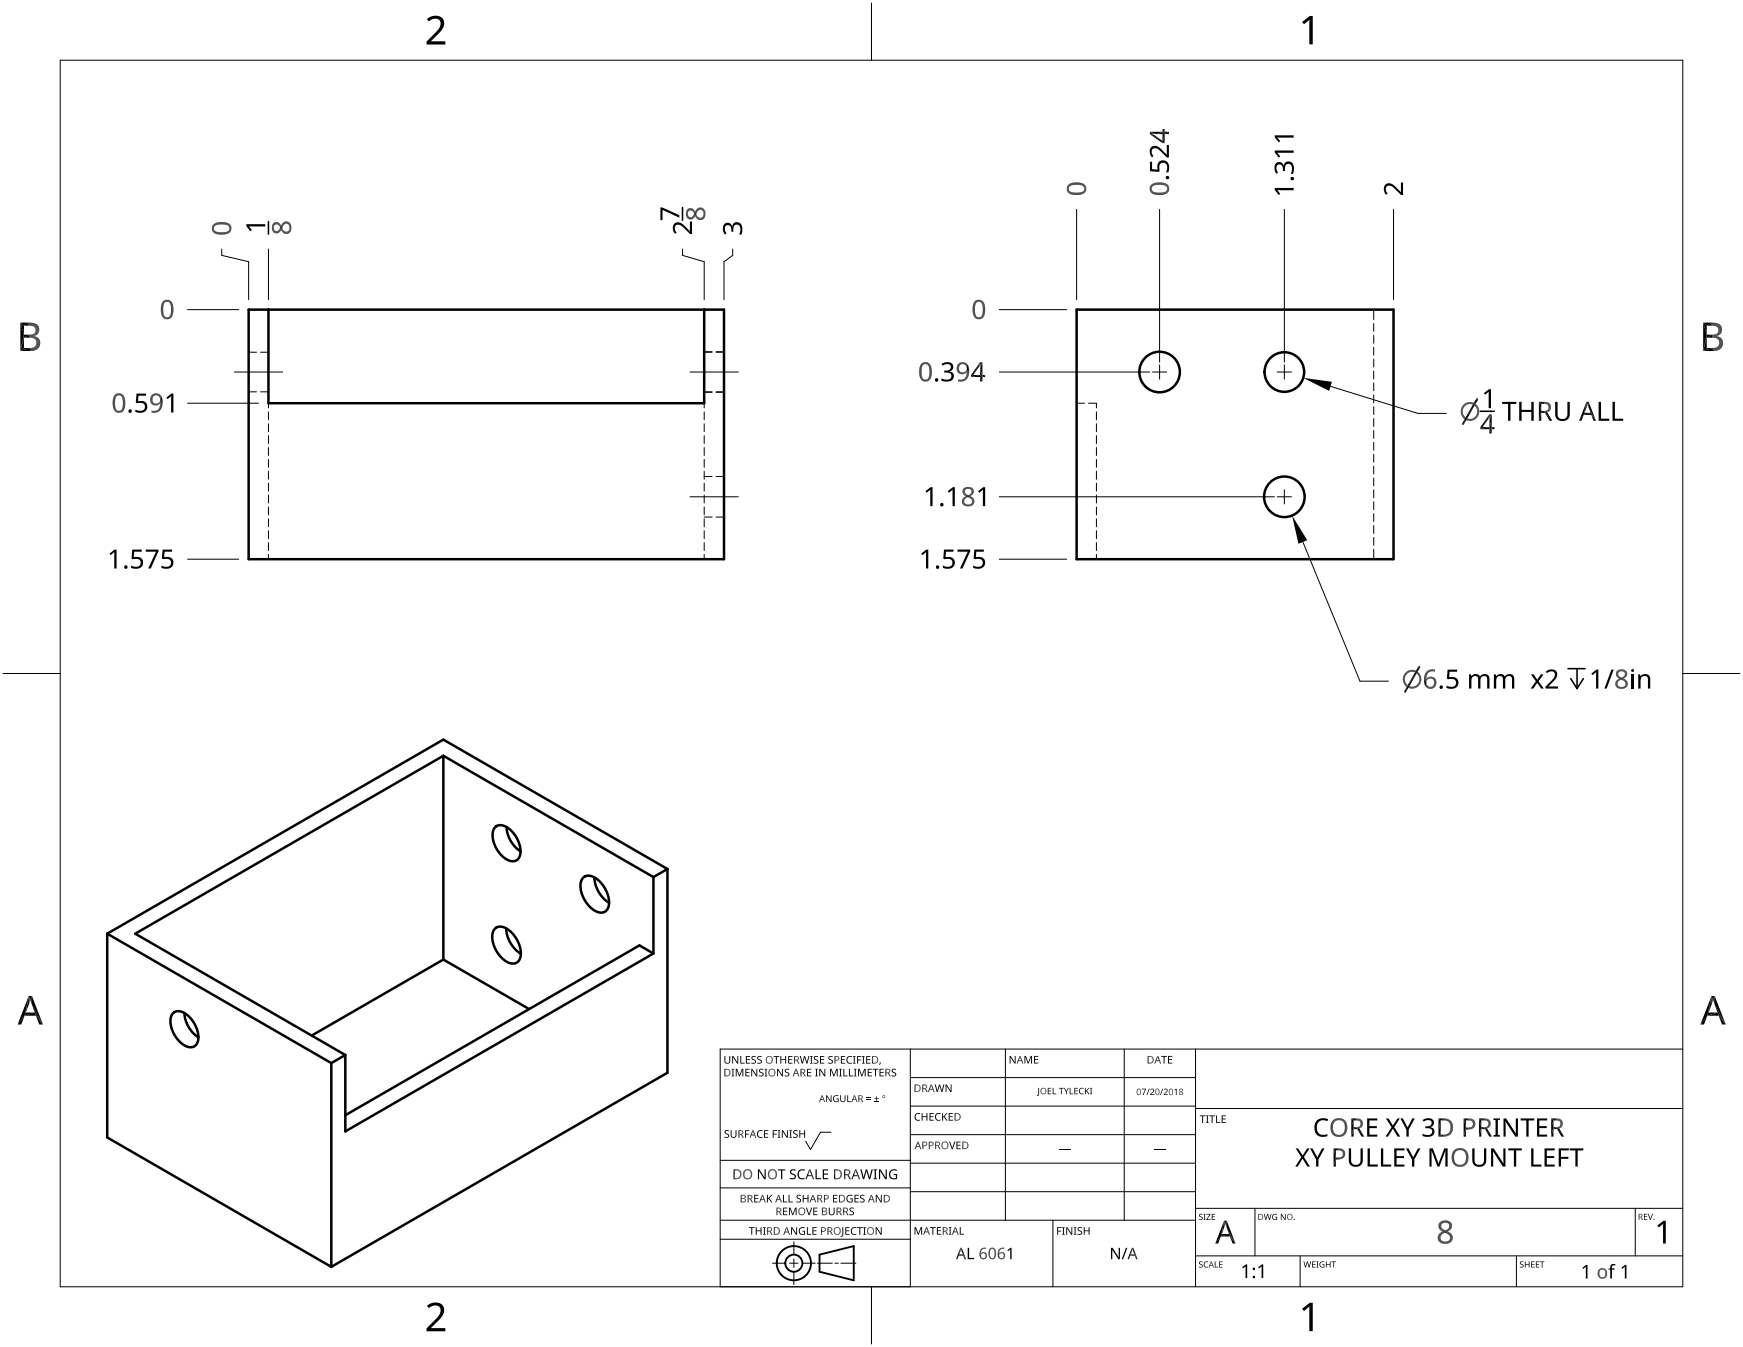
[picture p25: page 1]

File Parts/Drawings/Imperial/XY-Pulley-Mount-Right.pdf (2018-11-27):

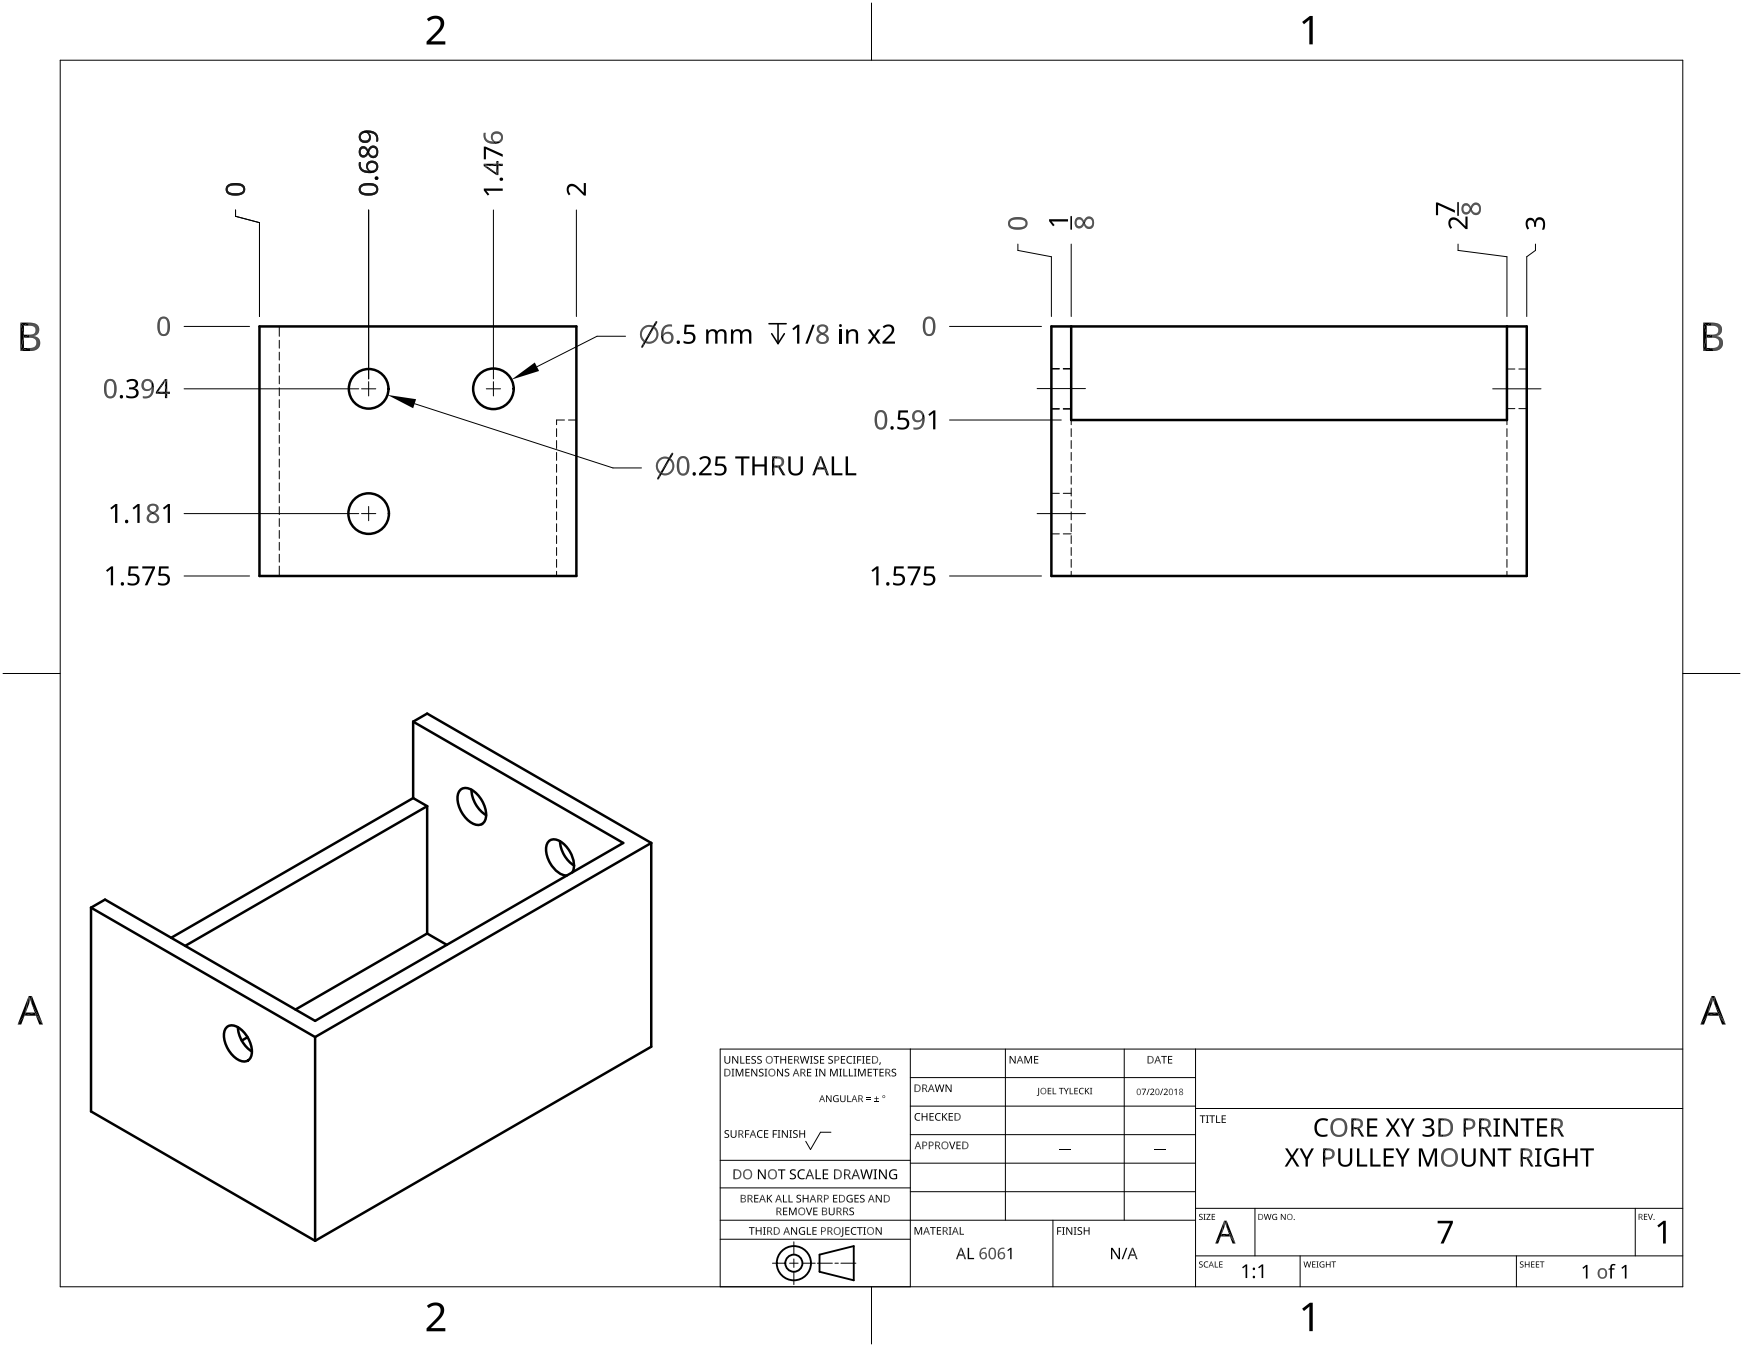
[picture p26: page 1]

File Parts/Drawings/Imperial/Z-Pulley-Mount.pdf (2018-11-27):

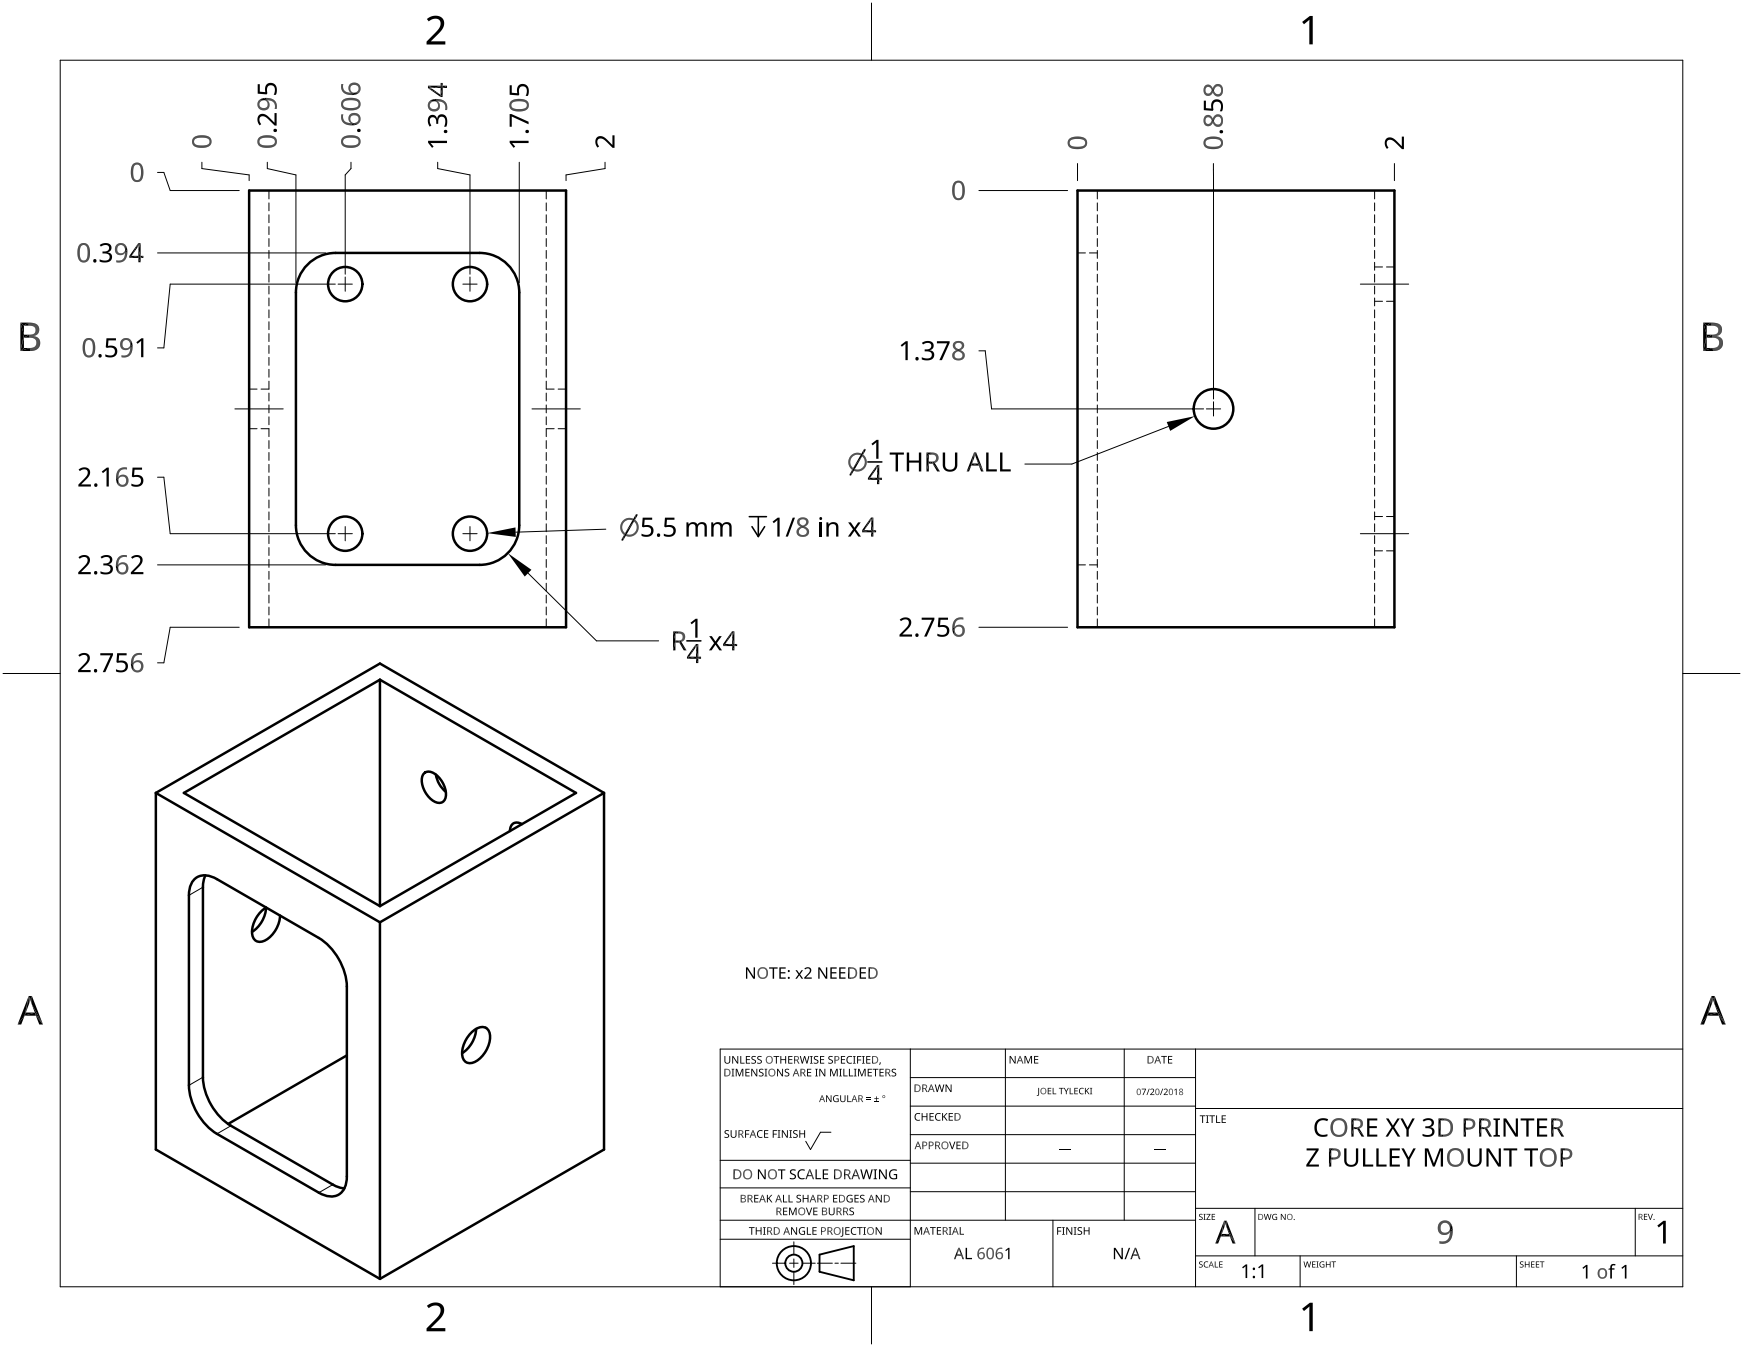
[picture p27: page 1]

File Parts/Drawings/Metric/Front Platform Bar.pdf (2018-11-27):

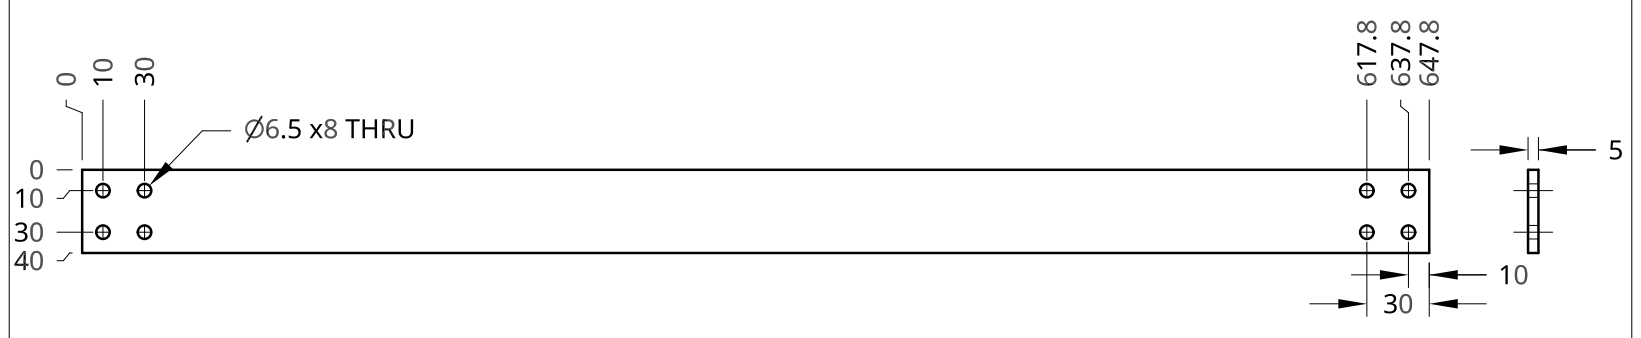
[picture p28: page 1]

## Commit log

2018-11-22 Upload STL Files
    [Bed Mount Wide.stl, Bed Mount.stl, Bed Stop.stl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]
2018-11-22 Organize part files
    [Bed Mount Wide.stl, Bed Mount.stl, Bed Stop.stl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]
2018-11-27 Update Titan Aero Mount
2018-11-27 Create Nema 23 mount.stl
    [Nema 23 mount.stl]
2018-11-27 Create Bobby-B-Bot Master Assembly.step
2018-11-30 Rework BOM
2019-02-19 Move Parts files
    [Bed Mount Wide.stl, Bed Mount.stl, Bed Stop.stl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]
